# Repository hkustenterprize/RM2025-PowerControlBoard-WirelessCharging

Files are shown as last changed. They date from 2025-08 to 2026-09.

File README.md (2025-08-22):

<div align="center">

# RM2025-超级电容与无线充电系统开源
## 香港科技大学ENTERPRIZE战队

</div>

> 论坛链接：https://bbs.robomaster.com/article/761385?source=8

以下为复制论坛内容



大家好呀，RM2025的超级电容和无线充电的开源报告终于写完了，这套前前后后做了三四个月，最后在用在了所有上场的车上（无线充只有步兵和英雄有），场上没出过什么问题，很稳定。硬件上与上一代开源没有很大变动，主要的改动是超级电容换了**峰值电流内环**，然后与无线充电进行了融合，放到了一个MCU上去控。虽然有一些缺陷和不足但是总体效果还可以，希望可以帮到大家。如果大家有任何有疑问或者发现有问题的地方欢迎随时联系！

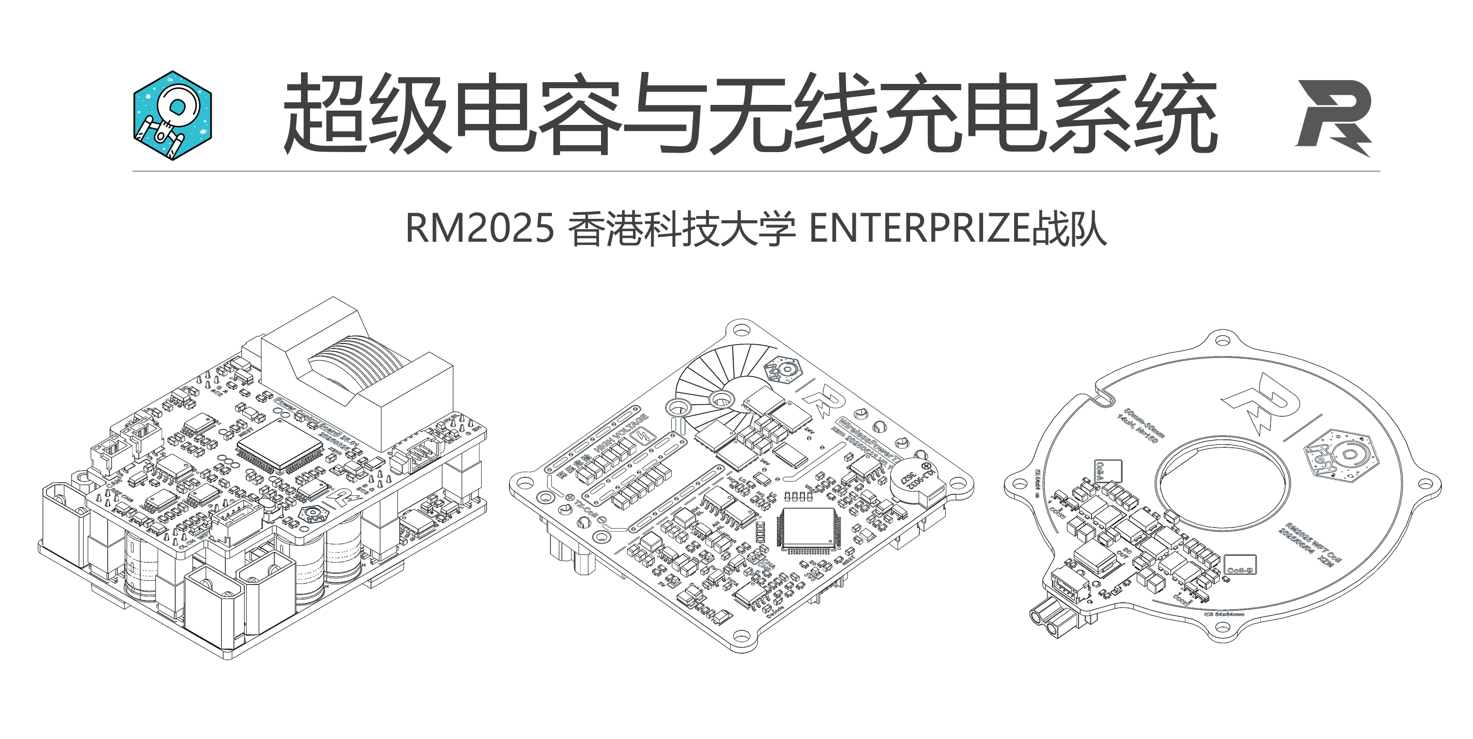
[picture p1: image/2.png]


> 欢迎加入开源交流QQ群：581184202

发射端/功控板硬件、功控板代码：xzm
> 联系方式：微信 xianziming0531，邮箱 zxianaa@connect.ust.hk

发射端代码：zzy
> 联系方式：微信 baoqi-zhong，邮箱 zzhongas@connect.ust.hk

## 前言

因为峰值电流调试起来比较复杂，也比较麻烦，所以大家有需要还是建议优先参考我们24年/23年的开源，这两版电容都是可以保证稳定的，24年的开源基本上板子做出了烧个代码就能用了。

硬件上整体改动不大，也是分了上下板的设计，下板加了一个用来无线充电的数控Buck，MCU换成了G474，为了峰值电流改了采样电阻的位置，然后根据写23赛季开源的学长的建议改了一下实现上管常开的方式，具体的东西都写在开源报告里了。

整体上场的效果还是不错的，电容响应很快，无线充电功率传输和反向通讯表现也很稳定（可惜复活赛输太快了没在比赛时充），今后有机会也会补充更多资料。无线充效果展示可以看 https://bbs.robomaster.com/article/760961 里面的视频。

## 工程文件

使用 KiCAD 8.0设计，可以点击下面的链接用 kicanvas 在线预览。

功控板上板：[<u>**点击预览**</u>](https://kicanvas.org/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)

功控板下板： [<u>**点击预览**</u>](https://kicanvas.org/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 )

无线充电发射端： [<u>**点击预览**</u>](https://kicanvas.org/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 )

无线充电接收端线圈： [<u>**点击预览**</u>](https://kicanvas.org/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 )

## 开源报告

见“技术报告” 文件夹

[**技术报告 PDF**](https://github.com/hkustenterprize/RM2025-PowerControlBoard-WirelessCharging/blob/main/%E6%8A%80%E6%9C%AF%E6%8A%A5%E5%91%8A/RM2025%E8%B6%85%E7%BA%A7%E7%94%B5%E5%AE%B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)

[**省流版 PDF**](https://github.com/hkustenterprize/RM2025-PowerControlBoard-WirelessCharging/blob/main/%E6%8A%80%E6%9C%AF%E6%8A%A5%E5%91%8A/%E7%9C%81%E6%B5%81%E7%89%88.pdf)

## 代码

功控板（超级电容+无线充电接收端）：待整理和测试，9月初整理过后的代码测好后开源

无线充电发射端：待整理，近期开源

## 相关开源
无线充电站机械结构：[ **【RM2025-无线充电站机械结构思路分享】香港科技大学ENTERPRIZE战队** ](https://bbs.robomaster.com/article/760961)

电容组：[**【RM2025-超小体积1980J电容组开源】香港科技大学ENTERPRIZE战队**](https://bbs.robomaster.com/article/760959)

## 复刻/已知问题/使用注意事项

1. 如果使用无线充电需要在功率控制板下板 无线充Buck的上管并联一个大功率肖特基二极管
2. 无线充电发射端的峰值检测二极管需要替换为肖特基二极管并联或其他快恢复二极管
3. 无线充电发射端的谐振电感需要自己绕，铁粉芯磁芯+利兹线
4. 使用手册和其他注意事项待完善，如遇问题欢迎随时联系

## 参考资料
1. 【RM2024超级电容控制器硬件+软件完全开源】 (史上最详细的开源！)香港科技大学ENTERPRIZE战队 https://bbs.robomaster.com/article/54127

2. 【RM2023-数控超级电容方案开源】香港科技大学-ENTERPRIZE战队 https://bbs.robomaster.com/article/9452

3. STM32 AN5306: Operational Amplifier (OPAMP) usage in STM32G4 Series

4. STM32 RM0440: STM32G4 series advanced Arm®-based 32-bit MCUs

5. STM32 AN5497: Introduction to the buck current mode with the B-G474E-DPOW1 Discovery kit（重要）

6. STM32 AN4539: HRTIM cookbook 

7. Qi Specification: Communications Physical Layer, Version 2.0 April 2023 

8. NXP AN4701: Demodulating Communication Signals of Qi-Compliant Low-Power Wireless Charger Using MC56F8006 DSC
STM32G474xB STM32G474xC STM32G474xE Datasheet 

## 致谢
感谢 ENTERPRIZE 战队硬件组学长 JYC RY OFR 为硬件部门打下的坚实基础，并在本赛季为超级电容与无线充电系统的设计调试中提供了巨大帮助

感谢 ENTERPRIZE 战队硬件组队员 ZZY 承担了大部分构建、调试发射端代码的工作

感谢机械组SJY帮忙画的保护外壳

感谢吉林大学、中国石油大学（华东）、华南理工大学在交流中分享的宝贵经验

非常感谢各位对香港科技大学 ENTERPRIZE 战队开源项目的关注与支持，若您在机器人设计过程中受益于我们的项目，恳请在开源引用中注明我们的项目来源。你们的支持是我们不断前行的动力。让我们携手共建一个鼓励创新、协作与超越的 RM 开源生态。







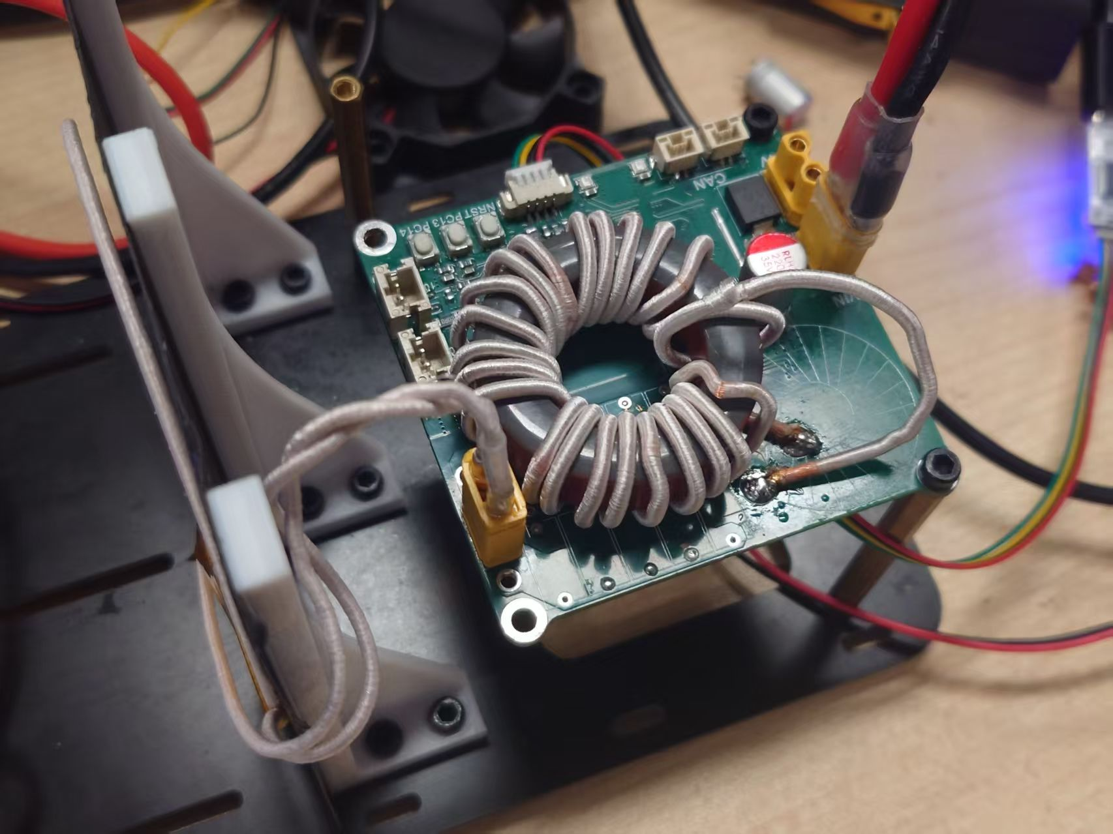
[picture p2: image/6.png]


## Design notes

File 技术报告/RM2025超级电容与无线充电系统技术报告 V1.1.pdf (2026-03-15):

1 / 96

# 超级电容与无线充电系统技术方案

RM2025 香港科技大学 ENTERPRIZE 战队

2026/03/16 V1.1

2 / 96

目录

3 / 96

开源报告版本：

V1.0 | 2025/08/08 | 首次发布
V1.1 | 2026/03/16 | 进行部分修正与补充，以 ** 标明

4 / 96

## 1. 技术背景概述

在 RM2025 的规则中，对于整车硬件要求大为提高。首先，总能量的限制的引入对电容控 制器的效率、响应速度等提出了更高的要求；其次，无线充电系统的加入使得底盘及超级电 容系统的架构变得更加复杂。

RM2025 赛季的一大变化是“能量限制”，与之前单纯的功率限制相比，能量限制对整车 设计要求再一次提高，从“开源”与“节流”两个角度分别来分析针对“能量限制”加入的 优化方法：

开源（增大可用能量）

- [硬件] 进行无线充电（在充电站以 120W 功率向电容组充入额外能量），详见“4. 无 线充电系统”
- [硬件] 提升比赛开始时的电容容量：例如比赛开始时电容组实际存入 1600J，实际可用

能量为 23000J+1600J=24600J，假设电容组的实际容量可以提升为 1900J，那么实际 可用能量也会相应提升，详见“3.6 超级电容组设计”

节流（减小能量损耗）

- [硬件] 进行动能回收，将刹车时的能量存入电容，详见“3.3.9 数字外环设计与实现”
- [硬件] 减小硬件损耗，如电容控制器、电容组、线损等等，在下文中将会重点讨论。详

见“3.2 硬件设计”

本文分为三部分探讨解决方案：整体硬件架构、超级电容系统与无线充电系统。

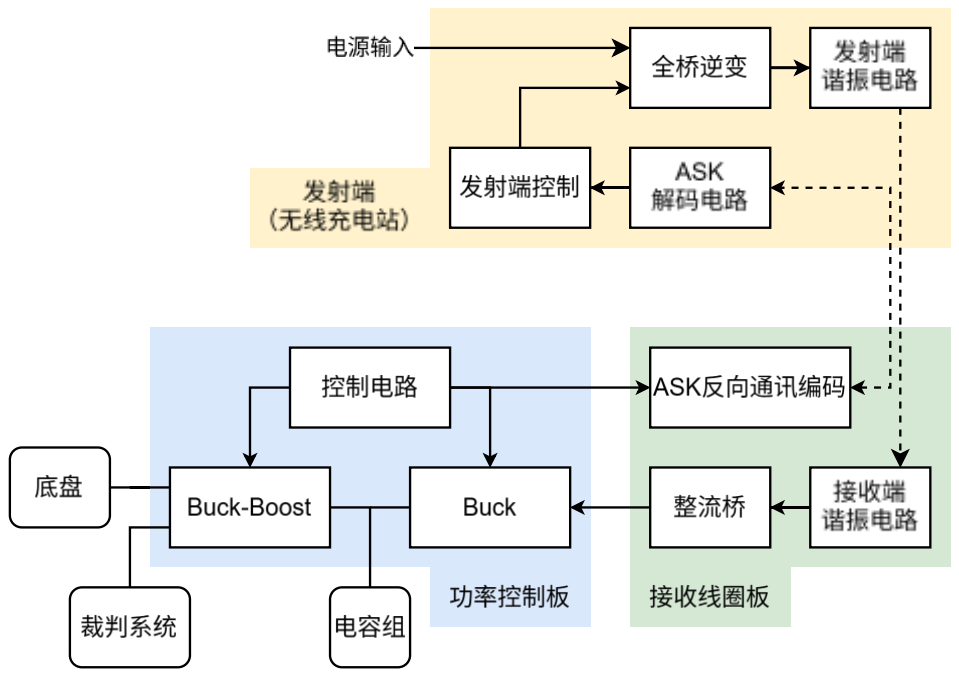
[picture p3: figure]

5 / 96

## ·2. 整体硬件架构

## 2.1 超级电容系统硬件拓扑

超级电容系统拓扑继续沿用上代电容控制器的双向 Buck-Boost 升降压架构，使得电容组 电压可以高于 等于或低于底盘电压，电容组最大电压值可以达到规则限制的 30V。由于电 容组电流受限于裁判系统超级电容管理模块 CM01 的 15A，所以电容组电压越高，理论最 大放电功率越大。以本设计中的 29V 电容组为例，其满电时理论最高可输出 435W 功率。

## 2.2 无线充电系统硬件架构

最大化无线充电系统的效率需要通过配谐来最小化无功功率，在 RM 场景下对无线充电系

统又以下要求：

- 无线充电系统的发射端体积可以较大，但接收端体积限制较为严格
- 在未对准时需要有较强的可靠性
- 发射、接收端间需要进行握手后进行充电
- 接收端需要能够处理 120W 的输入功率，并将其充入电容组中

在以上需求之外，为了简化硬件设计和接线难度，将无线充电接收端的相关电路与超级电容 系统融合，控制在同一块 MCU 上实现。

在考量上述因素并且查阅相关资料后，最终决定在功率传输部分使用 LCC-S 拓扑，激励源 选择全桥逆变，接收端的功率变换器选择 Buck 架构，将整流桥输出降压输入到超级电容中。

无线充电握手部分，选择通过模仿较为成熟的 Qi 协议的方法，通过 FSK 和 ASK 实现。

6 / 96

## 3. 超级电容系统

## 3.1 方案总览与主要创新点

峰值电流内环

25 赛季超级电容控制器的最大改变是实现了峰值电流内环控制，由模拟电路实现的峰值电 流内环理论上可以实现电感电流单周期达到设定峰值，配合简单的软件外环，其电流阶跃响 应可以达到 20us 级别。同时，纯模拟内环大大降低了 MCU 的运算负载，使得数字环路的 频率可以进一步提高，以实现更快的响应速度与更灵敏的保护。

峰值电流采样与平均电流采样共用放大器，最小化斜坡补偿

与峰值电流常见的在低位采样的设计不同，本设计在高位 MOS 处加入采样电阻进行采样， 将滤波电容放置于采样电阻后以采集电感电流。电流采样放大器输出直接连接到比较器的输 入进行峰值电流控制，同时也经过二阶低通滤波获得平均电流，并使用 ADC 采样用于软件 计算。这样的设计无需增加额外的采样电路，同时这样可以得到更多开关阶段的电感电流， 可以通过选择不同阶段的电流进行控制来最小化斜坡补偿的幅度。

充分利用外设简化电路

在具体实现上，得益于 STM32G474 的强大外设，硬件电路极为简化。峰值电流控制环路 的实现仅在电流感应放大器部分使用了 INA240A1 外置元件，剩余部分的环路，包括比较 器和 DAC 都在 MCU 内部实现；在电压检测中，通过使用 MCU 内置的运放的 Follower（跟 随器）模式，省去了外置运放，节约成本的同时简化了 PCB 布局。

充分利用外设减小软件运算量

在硬件层面外，25 赛季的超级电容系统充分利用 MCU 内部的不同外设间的互联矩阵，进 一步通过硬件外设替代软件计算。例如 OVP（过压保护）和 OCP（过流保护）通过 ADC 的 AWDG（模拟看门狗）实现触发保护，在进一步减小 MCU 的运算量的同时也加快了保 护的响应速度。在实际测试中，25 赛季超级电容系统的保护响应速度快于 24 年的设计，在 短路保护测试中尤其明显，短路产生的火花几乎不可见，且多次触发也不会损坏功率级电路， 证明了其优异的响应速度和稳定性。

无隔离电源上管常开

四开关 Buck-Boost 实现上管常开有助于提高转换效率。与使用隔离电源模块的传统做法不 同，25 赛季超级电容控制器的功率级利用拓扑本身的特性，使用了类似电荷泵的结构实现 上管常开，同时无需增加额外的控制芯片。无隔离电源的设计有助于减小静态功耗，使用隔 离电源模块时，静态功耗约为 2W，使用类似电荷泵的方式静态功耗仅有 0.8-1.2W 左右。

7 / 96

### 3.2 硬件设计

### 3.2.1 硬件设计总览

硬件上整体分为上下两块 PCB 板，上板为四层板，包含所有控制电路，下板为双层板，包 含超级电容和无线充电接收端的功率级，两板间使用 2.0mm 排针连接。

由于测试中发现下板功率级发热不大，故未采用铝基板，使得硬件设计更为自由（可以使用 直插电容、XT30 等通孔元件），并在板后粘贴一块 40x30x5mm 的散热片来辅助散热。将 发热网络（例如 MOS 管的 D 极）通过密集的过孔导热至 PCB 背面。

8 / 96

### 3.2.2 功率级

功率级为双向四开关 Buck-Boost 架构，分为 AB 两侧。本设计中将采样电阻放置于滤波电 容和高侧 MOSFET 间以对电感电流进行采样，当高边 MOSFET 打开时，采样电阻上的电 流等于电感电流，具体的峰值电流控制方式将在后文“3.3 环路与控制”部分详细介绍。

开关频率与电感选型

选择电感时，要在感值和饱和电流足够的情况下保证体积不会过大、且内阻尽量小。本设计 中电流双向流动，变换器的功率级一直处于 CCM 模式，控制上有四种工作模式（“3.3.6 时

序图”中详细说明），分别为 Buck、Buck-Boost(Vin<Vout)、Buck-Boost(Vin>Vout)、Boost。

定义 A 侧为输入端，由于 A 侧连接电管，电压范围即为电池电压范围，以使用 TB48S 为例， 电压最小为 22.2V，最大为 26.1V。B 侧为输出端，连接电容，电容电压范围为 0 - 30V。

选择开关频率为 250kHz，此频率下可以保证开关损耗不会过高、电感体积不会过大且不会 因为频率过高提升峰值电流控制的难度。适当大小的电流纹波会使得峰值电流控制更容易， 所以选取目标峰值电流为 4A 以内。

CCM Buck 模式下，电感电流纹波为: ∆IL =

Vout
L

(1 − DA

)

1
fs

=

Vin
Lfs

(1 − DA

)DA

当 DA = 0.5 时，∆IL 取最大值，Vin 最大为 TB48S 电池的 26.1V，因此：

∆IL,max =

26.1V
L×250kHz × 0.25, 令 ∆IL,max < 4A，L > 6.525uH

CCM Boost 模式下，电感电流纹波为: ∆IL =

Vin
L

(1 − DB

)

1
fs

=

Vin
L

(1 −

Vin

Vout

)

1
fs

当 Vout = 30V, Vin = 22.2V 时取得最大值：

∆IL,max =

22V
L×250kHz × (1 −

22V
30V

), 令 ∆IL,max < 4A，L > 6.96uH

CCM Buck - Boost 模式下，设计一侧占空比为 0.84，另一侧小于 0.84（后文会详细展

开），此时 Vout ≈ Vin ≈ 24V, 估算电感电流纹波为：∆IL =

24V
L

(1 − 0.84)

1
fs

令 ∆IL < 4A，L > 3.84uH

9 / 96

B 侧由于输出电流会受到裁判系统电容管理模块 CM01 的 16A 电流限制，实际最大电感电

流为 Boost 状态下 Vout = 30V,Vin = 22V 时取得，此时：

IL,peak = 16A × Vout⁄Vin + 0.5∆IL < 22.5A

考虑留有一定余量，选择电感饱和电流至少为 25A

最终，选择 10uH VER2923 电感，饱和电流 30 - 37A，DCR 约为 2.5mΩ，损耗较小，最 大电流纹波小于 3A，满足设计要求。

电容选型

选择电容时，假设最大电流纹波为 3A，由于 Buck-Boost 模式下电感电流波形近似为梯形， Boost 或 Buck 模式下近似为三角波，所以在电流纹波相同时最大电压纹波在 Buck-Boost 时取得（积分电感电流与平均电流的差值最大），可以估算输出纹波一定小于：

∆Vout <

T
2

×

Ipp
2

×

1

Cout

。

在采样电阻后每侧使用 4 个 10μF 50V MLCC 电容和 2 个 220μF 35V 固态电容分别进行低 频和高频滤波，此时输出纹波理论最大不超过 50mV，符合设计要求。

在 PCB Layout 时将高频功率环路（MLCC 电容 - 采样电阻 - 半桥 – 地平面）面积最小 化，并在保证过流能力足够的情况下最小化两侧 SW 的面积来减小干扰。

采样电阻选型

采样电阻选用 2mΩ 2512 的合金电阻进行电感电流，选型时主要有以下考量：

- 考虑损耗时，采样电阻不能太大。2512 电阻的最大功率为 3W，以最大电感电流 25A

计算，Rmax = Pmax Imax

2 ⁄ = 4.8mΩ，且相对 NMOS 内阻 (5.5mΩ) 不能太大

- 考虑采样时，采样电阻不能太小。采样电感电流需要较高带宽的电流感应放大器，而一 般放大倍数越大的放大器带宽越低、噪声越大，限制了放大倍数不能很大。由于 ADC 的精度限制，采样电阻阻值太小会导致分辨率过低。结合使用的电流感应放大器

10 / 96

INA240A1（选型在后文“3.2.5 采样与反馈”会提到）的 20V/V 放大倍率，最终选择

2mΩ的采样电阻。

最终 ADC 采样值理论计算公式为（ADC 分辨率 12bit）：

ADC Value = I × 2mΩ × 20 V⁄V × (4096⁄VREF)

理论分辨率和量程为 (VREF 取 2.9V) ：

Ires =

2.9V × 1
2mΩ × 20 V⁄V × 4096 = 0.0177A

Irange = ±

2.9V⁄2
2mΩ × 20V⁄V

= ±36.25A

功率 MOSFET 的选型

对于功率 MOSFET，要在保证 VDS 耐压余量足够的情况下，取得栅极电荷量、导通内阻间

的平衡。这里沿用 2024 赛季队内开源的选型 BSC066N06NS：其耐压为 60V，高于两倍最 大电压，防止电压过冲损坏 MOS；栅极电荷小于 20nC，保证较低的开关损耗并缩短死区

时间，防止在 VDS 较高时超过 SOA；Vgs = 10V 时 Rdson 为 5.5mΩ，损耗较小；持续电 流 64A、峰值 256A，远大于正常运行需求，保证了足够的安全余量。

其他设计

两侧滤波电容后各放置有一对 TVS+保险丝的保护电路，此电路可以在电流失控、输入输出 反接或过压等情况时熔断保险丝。保险丝选型为 1808 封装的 20A 快断保险丝，内阻约为

1.5mΩ。

A 侧在保险丝后有另一个 2mΩ 的采样电阻，用来采集裁判系统端的输入电流，此处虽然电 流更小（最大约为满级功率时 5A 左右），但是考虑到简化 BOM（防止错焊、减少备料种 类等）且分辨率足够的情况下保持相同的采样电阻和电流感应放大器的配置。

将采样电阻放置于保险丝后的设计可以保证即使在超级电容系统发生严重故障、保险丝断开 时，底盘也可以直接被裁判系统供电，且整个超级电容系统完全断开。

11 / 96

### 3.2.3 驱动级

栅极驱动芯片选型

栅极驱动芯片选用 UCC27201A 或者其平替 SLM27211。虽然 UCC27201A 性能稍弱于

UCC27211，但后者非常容易买到假货，且 UCC27201A 3A 的推挽能力在 250kHz、功率

MOSFET 栅极电荷不到 20nC 的已经足够，所以选用 UCC27201A 作为栅极驱动。后来经 过测试发现 SLM27211 稳定性足够且价格更便宜，于是在后续版本换用 SLM27211。

栅极驱动电路

栅极驱动电路以 UCC27201A 为核心，贴近 VDD 引脚放置一个 4.7μF 50V 电容，保证在开 关瞬间不会因为寄生电阻过大导致 VDD 电压突降而使芯片进入 UVLO 保护。在输出引脚 HO 和 LO 各串联一各栅极电阻，防止过快的开关导致电压过冲，此电阻需要通过测试反复 调整为合适的值，这里取 3.3Ω。自举电容按数据手册选用 100nF 0603 50V 电容。

布局中要尽量缩短高 di/dt 回路，尤其是栅极的走线要尽可能粗且短，输入电容要贴近芯片 的 VDD 引脚并保证地的连通性较好。

为了保证 MOSFET 的 Rdson 较小，设置驱动电压为 10.8V。过高的电压会使栅极电荷增大， 过小则会加大 Rdson，考虑到数据手册推荐电压为 10V 和高频开关中寄生参数的损失（上 管自举电容充电二极管的压降等），设计驱动电压为 10.8V

12 / 96

### 3.2.4 上管常开实现方式

在输出与输入电压有一定差距后，Buck 或 Boost 模式较比 Buck-Boost 更为高效，但如果 一侧上管直接常开，由于 G 与 S 级间漏电等原因，上管会渐渐转为不导通状态，所以要实 现上管常开必须采用一定方法保持上管栅极电压不变。

现有方案参考

队内 2023 和 2024 赛季的解决方案为引入两个隔离电源模块，输入为 10.8V 和 GND，输出 负连接到 SW，正连接到 HB（自举电容两侧），这个方案的优点是设计较为简单，但是即 使隔离电源输出电流很小，也会有较大的静态功耗（在本赛季这个问题会被放大）。

另一种解决方式是在上管常开一侧以较低的频率进行开关充电，例如对侧开关 500 次，常 开侧进行一次占空比为 0.95 的开关，并配合增大的自举电容实现上管近似常开。这种方案 的优点是没有引入额外的静态功耗，且无需额外硬件上的改变，但是软件上实现较为复杂。

本系统使用的新方案

在本方案种则使用了一种类似电荷泵原理的方式实现上管常开。如图，其中 BAV99 为 100V 耐压、SOT-23 封装的开关二极管（其实就是两个二极管合在一起），BZT52C11S 为齐纳 电压为 11V±0.6V 的稳压二极管，两个 10kΩ 电阻为限流电阻。输出连接到自举电容两端。

** 此处 R11 的阻值建议修改为 33ohm 左右，防止充电不足

此电路工作原理主要依赖一个特性：常开侧对侧的电路一定在进行开关，例如 Buck 工作时

A 侧进行 250kHz 的开关，B 侧常开，Boost 同理。

原理分析

以如图 Boost 工作、输入电压 24V、输出电压 24V（理论上最不理想的电压）需要 A 侧上 管常开时为例，工作分为两阶段：

B 侧下管打开，此时 B_SW 为 0V，电容 C12 通过 R11 电阻与 D11 左侧二极管充电，

此时 D11 右侧的二极管截止。在稳态运行中，C12 的电压为 10.8V – 0.8V = 10V。

B侧上管打开，此时B_SW为24V，A_SW为24V，C12上端电压约为24V + 10V = 34V， 此时如果自举电容电压较低，则 C12 通过 D11 右侧的二极管与 R12 电阻向自举电容充 电，同时通过稳压二极管限制自举电容两端电压为 11V 左右，稳态运行中自举电容可

13 / 96

以至少可以被充电至 9.2V 左右，即高侧开关 Vgs 至少会保持在 9.2V 左右。

不考虑漏电，实际运行中因为常开侧电压一定小于开关侧，且差距一般至少为 2V（否则进 入 Buck-Boost 模式），常开的上管的 Vgs 一定可以维持到稳压二极管的电压（11V 左右）。

漏电与充电理论计算

上管常开时，栅极漏电的来源有 (1)MOSFET 本身 (2)稳压二极管 (3)自举电容 (4)驱动芯

片，经查阅数据手册，其最大值分别为 (1)100nA (2)0.1μA (3)~5nA (4)1μA，加和为μA 级 别，且驱动芯片正常漏电为 0.0005μA，与最大值相差较多，实际漏电电流远小于估算值。

正常运行时，假设 C12 两端电压为 9.9V，自举电容两端电压为 9.0V，开关二极管压降为 0.8V (10mA)，则单次开关的充电能力为（两阶段一致）：

Q = ∆V (1 − e
−

t

RC) C = (10.8V − 0.8V − 9.9V) (1 − e
−

2μs
4.7μF×10kΩ) × 4.7μF ≈ 0.02nC

此时平均充电电流 I ≈

0.02nC
4μs

≈ 5μA 大于漏电流最大值，由于估算条件极为保守，实际充电

电流会显著大于估算值。

静态功耗分析

估算静态功耗时，假设自举电容稳定在 10V，充电电流忽略不计，功耗近似为：

PDC = |VA − VB

| × (|VA − VB

| − 11V)⁄20kΩ

可以看出最大静态功耗为 A 侧 24V B 侧 0V，电容刚刚开始充电的场景，此时功耗约为 0.016W 且只有单侧上管常开电路有功耗，在正常运行电压范围（B 侧 10-30V）时静态功 耗极低，仅有 mW 级别，可以忽略不计。

结论与实际测试

综上所述，本电路理论上可以十分稳定且低功耗地实现上管常开，实际测试中栅极电压可以 稳定在 10V 左右。Buck 和 Boost 状态下都可以稳定运行。对比隔离电源模块的方案，25 赛季采用的新方案使得整体静态功耗从 2W 降低到 0.8W-1.2W 左右，并缩小了元件所占体

积。

14 / 96

### 3.2.5 采样与反馈

总体需求分析

超级电容系统中，需要采集 5 个物理量作为控制依据，分别为：两侧电压 VA、VB，两侧电 流 IA、IB，裁判系统端电流 IR。其中两侧电流需要特殊处理，峰值电流需要电感电流的波

形，而 ADC 需要采样其平均电流。

为了提高响应速度，软件外环的运行频率为 62.5kHz (开关频率/4)，每开关周期一采样，所 以需要采样电路滤波有较高截止频率。数控电源滤波频率一般取开关频率的 1/10 到 1/20， 考虑到提升响应的需求，适当选择较高频率，接近 25kHz 左右。

由于 STM32 的 ADC 采样时近似于给一个小电容充电，所以如果条件允许则在 ADC 引脚前 放置一个小电容，防止采样时间过短产生误差，或使用运放进行跟随来减小阻抗。

参考电压

采样电路与 ADC 需要精确的参考电压以保证结果的稳定与一致。如果直接使用 LDO，即使 在进行校准后也无法避免温度和输出电流等因素导致的电压漂移。所以在本设计中使用了 STM32G4 系列内置的电压参考，省去了独立的参考电压芯片。

STM32G4 系列内置高精度电压参考，有 2.048V 2.5V 2.9V 三个电压挡位，本设计中选用 2.9V 挡位，其精度标称为±4mV，理论精度 0.14%，意味着测量功率时由参考电压造成的

误差最大为 0.276%。

为了给电路感应放大器提供参考电压，将 MCU VREF+引脚输出的
参考电压经过 MCU 内部运放跟随后的输出作为参考电压输出，同 时在 VREF+引脚和最终输出的 VREF 网络都使用电容进行滤波和

稳压。

电压采样电路

电压采样首先使用 33k 和 2.2k 电阻分压，与 3.3nF 电容组成一阶滤波，设计参数如下：

直流缩放倍率：GainDC =

2.2kΩ
2.2kΩ+33kΩ

=

1
16

V⁄V

最大量程：Vmax = VReference⁄GainDC = 2.9V × 16 = 46.4V

一阶滤波截止频率：fcutoff =

1
2πReqC

=

1
2π(33kΩ∥2.2kΩ)×3.3nF

≈ 23.38kHz

ADC 理论分辨率：Vmax⁄4096 = 11.328mV

滤波后的信号进入 STM32G4 内部运放的输入，内部运放配置为 Follower 模式，并将运放

输出连接到 ADC 输入。内置运放的 Power Mode 配置为 High Speed，可以提供 45 V/µs 的压摆率，更适合处理高频模拟信号。

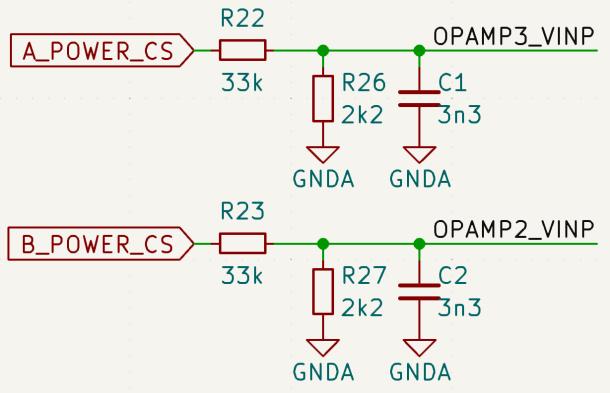
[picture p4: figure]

15 / 96

电流感应放大器的选择

峰值电流控制需要获得波形较为精确的电感电流，这就对采样带宽提出了很高要求，而其电 流绝对精度要求不高，所以选择放大器时基本仅需重点关注带宽和压摆率（例如 LM51770 的电感电流采样放大器带宽为 1Mhz），配合低位采样即可较好地获得相对精确的电感电流 波形。而 ADC 采样的平均电流对带宽要求不高（一般为开关频率 1/10 到 1/20 左右即足够）， 但却对绝对精度要求较高，选择放大器时需要重点关注误差、漂移和噪声抑制等参数。同时， 由于电流双向流动，需要选择支持双向电流采样或带有 VREF 引脚的电流感应放大器。

综上所述，本方案的做法虽然电路简单，但是对电流感应放大器要求较高，需要同时具备高 带宽、高共模电压、低误差、低漂移和噪声抑制等特性。由于符合要求且带宽 800kHz 以上 的电路感应放大器价格较高（例如带宽 1.1Mhz 的 INA241A1 价格接近 20 元/片），所以在 测试 INA240A1 后发现其带宽足以稳定实现峰值电流控制后，选用其作为电流感应放大器。

INA240 系列共有 A1-A4 四种型号，为了减小噪
声，选择增益为 20V/V、标称带宽为 400kHz 的
A1 型号。通过数据手册中的增益-频率图可以看出

在 1MHz 频率下 INA240A1 仍可以保持 10dB 的 增益，由于峰值电流控制并不需要增益很准确的
高频信号，故其可以稳定实现峰值电流控制，与
测试结果相符。

16 / 96

电流采样电路

峰值电流控制模式需要对电感电流进行采样，使用上文提及的 2mΩ 电阻，在上板使用 INA240 电流感应放大器将采样电阻两端差分电压转化为单端电压输出。电感电流信号连接 比较器进行峰值电流控制，同时经过二阶 RC 滤波得到平均电流并通过 ADC 采样以进行软 件环路控制。

与将电感电流采样与平均电流采样分离的设计不同（如 LT8705 等），本方案的设计可以通 过单一电流感应放大器同时获得电感电流与平均电流。这种做法很大程度上简化了电路，核 心部分仅需两个电流感应放大器，并且无需引入额外的采样电阻，减小了损耗。

通过第一版硬件的测试发现一阶 RC 滤波的 ADC 采样结果噪音较大，所以在第二版中使用 了二阶 RC 滤波，可以实现在截止频率后-40dB/dec 的衰减。参考电压源分别连接到 2.9V 的参考电压和模拟地，实现 1/2 参考电压的输出偏置以实现双向电流检测。具体理论设计参 数如下：

直流缩放倍率：GainDC = 2mΩ × 20V⁄V = 0.04V⁄A

单向最大量程：Vmax = 0.5VReference⁄GainDC = 0.5 × 2.9V⁄(0.04V⁄A) = ±36.25V

二阶滤波截止频率： fcutoff ≈

1
2πRC

=

1
2π×2.2kΩ×3.3nF

≈ 21.92kHz

ADC 理论分辨率：2Vmax⁄4096 = 17.70mA

17 / 96

对于裁判系统电流采样，由于其采样直接为平均电流（采样电阻两侧均有滤波电容），噪音 较小，故使用一阶 RC 滤波即可得到噪音较小的数据，其余参数与上文一致。

模拟电路 PCB 布局

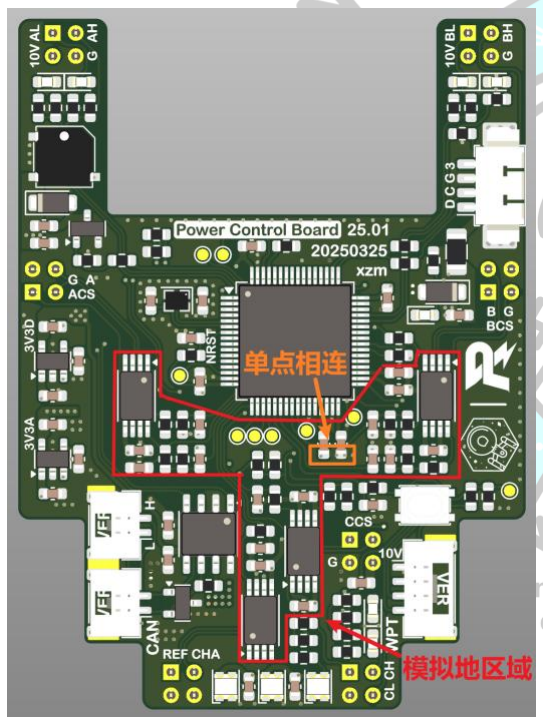
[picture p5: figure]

由于超级电容的 PCB 上同时由敏感的模拟采样电路、数字电路和大功率的功率开关电路， 对 PCB 布局由较高要求。首先电容控制器分为上下两板，将大功率地和数字地进行了分割； 在上板上对模拟部分的地做了分割，并在 MCU 的 VDDA/VSSA 滤波电容处单点相连。

18 / 96

对于电流采样，差分信号线从采样电阻开始使用开尔文接法，通过排针来到上板并继续保证 等长差分，同时保证其不与相同网络其他处有连接，保持由采样电阻到放大器完全独立。

对于电压采样，由于排针体积 Pin 数的限制，在板对板连接处辅助供电输入端共用同一引脚， 在上板排针焊盘处分离，分别走向电压采样电路和辅助电压输入。

校准
尽管前文提到的各种设计已经尽量消除误差，但由于各种因素（例如 ADC 精度、温度、放 大器误差等）导致的误差仍然不可忽略，所以使用一次函数对 ADC 采样结果与真实值对比 进行拟合，实测可以极大提升采样精度。例如下图为采样电压的校准拟合：

实际使用中对每个焊接的电容控制板的五个测量量分别进行校准，校准结果统一存储在

Calibration.hpp 文件中，并根据 MCU 内部的 96 位 UID 进行编号，保证任意电容控制板只 需要进行一次校准且不会因为烧错代码使用错误的校准信息。

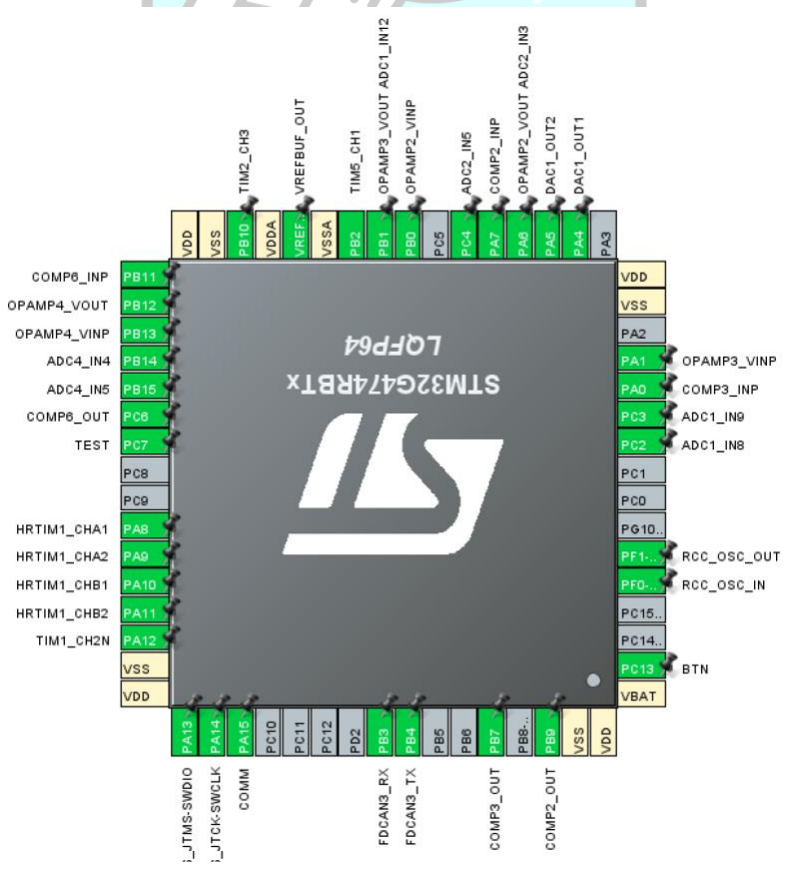
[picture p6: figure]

19 / 96

### 3.2.6 MCU 与控制

MCU 选用 STM32G474RBT3。STM32G474 提供了功能极为丰富的高精度定时器（HRTIM V2），使得峰值电流控制成为可能；170Mhz 的主频也使得环路计算可以更快；丰富的模拟 外设（电压参考、内置运放、比较器、DAC 等）使得外围电路得到极大简化；同时，选用 RBT3 版本使得其耐温达到-40°C 到 125°C，提高稳定性。

MCU 采用 LDO 供电，并在每个供电引脚配备 100nF 电容。晶振选用 2012 封装的 25Mhz 晶振以减小体积和干扰，PCB 上对晶振本身和其走线进行了包地处理、并在所有层禁止其 他走线来防止干扰。

由于实际使用中对于 BOOT0 和 NRST 按钮需求极小，故移除独立按钮，仅保留下拉与上 电复位电路。保留一个连接到 GPIO 的按钮进行交互。

STM32CubeMX 中的部分引脚配置如下（不包含无线充电部分）：

20 / 96

### 3.2.7 辅助供电

电源框图

超级电容及无线充电系统共有三个电压源，分别为底盘端电压、电容组端电压、无线充电输 入端电压。为了保证任意电压源有输入时系统都能工作，使用三个二极管分别从三个电压源 指向辅助供电 Buck 的输入，因为辅助电源功率很小，使用普通肖特基二极管即可。同时为 了烧录及调试方便，将 SWD 的 3.3V 输入通过保险丝和 TVS 保护后通入 3.3V 网络。

辅助电源电源网络

电源网络名称 | 描述 | 用电器
10V | MOS 栅极驱动电源 | MOS 栅极驱动芯片
5V | 5V 主供电 | CAN 收发器、蜂鸣器、LDO 等
3.3V | 3.3V 主供电 | MCU、CAN 收发器
3.3VA | 模拟 3.3V 供电 | MCU VDDA、电流感应放大器

取电位置

虽然辅助电源的功耗较小，但其电流仍然不可忽视，所以需要选取合适的取电位置来避免对 功率级电流测量的干扰。如图为超级电容系统功率电电路的框图：VREF 为裁判系统电源管 理模块的 Chassis 接口输出，通过裁判系统电流检测电阻后输出到底盘；底盘网络通过保 险丝进入 Buck-Boost 电路的 A 侧，在通过两个电流检测电阻、功率级后再经过保险丝进入 电容组。

实际辅助电源的 VA、VB 输入分别接入如同所示中的 VA_CS 和 VB_CS 网络。对于 A 侧， 在 VA_CS 处取电可以避免辅助供电输入绕过裁判系统电流检测电路，使得测得的裁判系统 功率不准。不在 VA 和 VB 处（采样电阻后）取电可以避免随功率级的电流采样造成干扰。

21 / 96

Buck 部分电路

Buck 芯片选用 RY8411。输入电压最高 42V，可以保证在功率级电压不超过 30V 的情况下 有充足的余量；输出电流最大 1.2A，远超辅助供电的需求；同步整流可以提供较高的效率

并且无需续流二极管、减小了电路面积。

输入部分采用三个耐压 40V，最大电流 3A 的肖特基二极管（K34），并且在经过 1A 的保 险丝后进入 Buck 芯片的输入；其中无线充电输入端（C_POWER）独立使用一个保险丝是 为了布局方便。每个 Buck 芯片输入各使用两个 1206 封装耐压 50V 的 10uF 电容，输出各 采用三个 0805 封装耐压 25V 的 22uF 电容，由于 X7R/X5R 材质的电容实际容值随着两端 直流电压的升高而降低，所以选用高耐压电容来减小容量衰减。电感选用 3015 封装的 4.7uH 电感，虽然其 DCR 较大（约为 100mΩ级别）且饱和电流较小（约为 1.1A），但对于辅助 供电来说已经足够。

22 / 96

布局上将全部功率回路在顶层布局完成。保证输入电容 - 芯片 - 输出电容的 GND 回路阻 抗较小，且输入电容距离芯片的 VIN 和 GND 尽可能近；自举电容高频回路紧挨芯片的 SW 和 BST 引脚减小干扰，电感布局保证 SW 的网络面积尽量小防止干扰；反馈回路在输出电 容后通过内层独立走线连接至采样电阻处，且保证 FB 网络面积尽可能小避免干扰。

LDO 部分电路

LDO 选用 RS3236，输入电压最大 7.5V，输出电流最大 500mA，都有较大余量。电路基本 参考数据手册，在 BP 引脚连接 10nF 电容来减小输出噪声。

PCB 布局上依然在同一层完成了功率回路的走线，保证输入和输出电容的两端离芯片尽量 近，为了防止 EN 引脚走线切割 GND，将其从内层接入芯片。

SWD 电源输入

由于电容控制器烧录及调试代码频率较低，对于 SWD 供电的处理和保护较为简单，通过 1A 保险丝和 3.3V TVS 进行防护，并使用一个 4.7uF 电容进行滤波。

23 / 96

### 3.2.8 通讯与交互

通讯部分采用 CAN 协议，直接接入底盘的 CAN 网络并与主控板进行通讯。收发芯片选用

SIT1042T/3，输出采用 ESD1CAN 进行防护。

交互上使用一个按钮进行重启和清除故障等操作，通过 WS2812B 进行状态指示。按钮使用 一个 RC 滤波电路来消抖，引脚使用 GPIO 内部上拉。WS2812B 选用 2020 封装减小体积。

### 3.2.9 成本控制

为了节约经费，超级电容控制器在设计上进行了最大程度的精简，例如前文提到的用 MCU 内部运放代替独立运放芯片等。同时，对于电阻或电容取值较宽松的地方进行了取值的统一， 在不同电流采样处统一采样电阻和电流感应放大器的选型，最大程度简化 BOM。 本赛季考虑全阵容+备车+备件的需求大致需要 8 套电容控制器，使用嘉立创经济型 SMT 贴 片核心板的电阻电容，其他元件和下板全部手焊，可以控制整套控制器成本在 100 元左右。

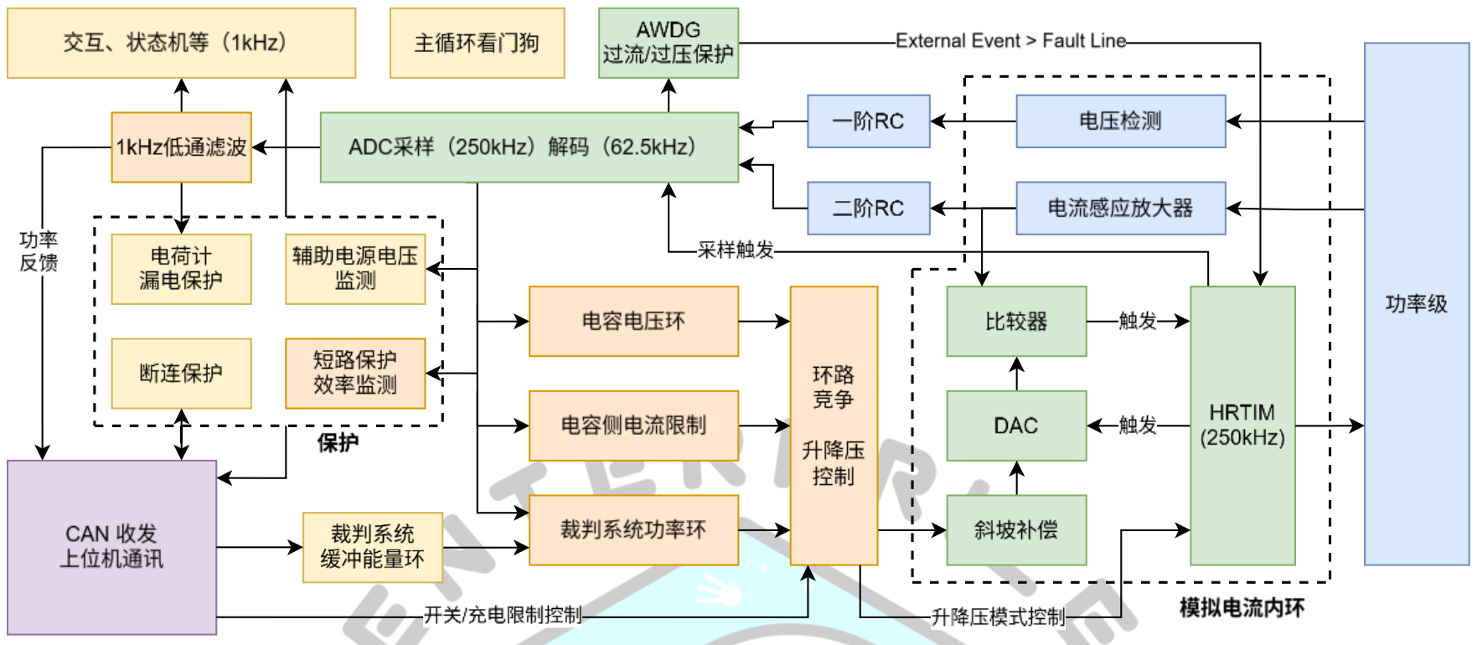
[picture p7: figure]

24 / 96

## 3.3 环路与控制

### 3.3.1 整体控制框图

如图，本方案使用 STM32G474 作为整体控制核心。其中使用了大量 MCU 内部外设来简化 硬件设计、加快软件运行速度。

### 3.3.2 控制系统整体需求分析

本部分主要基于 Buck-Boost 拓扑分析 RoboMaster 竞赛场景中超级电容系统的控制需求。 如图为简化的功率级框图，整个控制器共有三个功率端口，分别为：
- 裁判系统电源管理模块 Chassis 接口输出（下文简称 Referee/R 端）
- 底盘电机输出接口（下文简称 A 端）
- 电容组接口（下文简称 B 端）

在下文中将从限制因素入手，分析理想中的控制效果及实现方式。

25 / 96

限制因素

对于裁判系统 R 端（0V 或电池电压）：

- 比赛规则限制此接口输出的功率上限，功率计算方式为 R 端的电压×电流，其中电压为 电池电压，此功率上限一定不能超过，否则会导致判罚。
- 由于裁判系统电源管理模块无法检测负功率（不会返还反向流入裁判系统的能量），所 以理想情况下要保持此接口功率一直为正，即保证此接口只会输出能量。
- 虽然有功率限制的存在，但理想情况下控制器需要有完全吃满裁判系统功率限制的能力 以保证性能。

总结：R 端一定要保证不超过功率限制，最好保证功率不倒灌，最好可以吃满功率，电压输 入范围为电池电压

对于底盘端（与 R 端电压一致）：

- 此端口功率受上位机控制的电机决定。
- 此端口的瞬时功率较大，例如电机急停时会有巨大的反冲功率灌回系统中，系统必须反 冲有较强的处理能力，否则其将不受控制地流回电池，造成浪费。

总结：底盘端会承受较大瞬时功率，且系统无法控制接口的输出输入能量

对于电容组端（0V-电容组最大电压）：

- 此端口电压绝对不能超过电容组的最大电压，需要严格限制并保护。
- 由于此接口与裁判系统电容管理模块 CM01 直接串联，此端口的电流不能超过 CM01

的电流限制（±15A）。

- 此接口电流不能超过电容组最大充放电电流，并且在电容电压较低时需要进一步限制电 容组的充放电电流。由于电容组的最大电流一般很大（30A 级别），远大于 CM01 的限 制，所以这里只需要考虑低电压限制电流的情况

总结：电容端需要有严格的电压电流限制，并且在电容组电压低时要进一步限制电流

对于功率级本身，任意时刻电感电流不能超过饱和电流（约 30A 级别）

26 / 96

工况分析

| 底盘需求功率低 | 底盘需求功率高
电容能量低 | 快速充电 | 提供尽量多的功率，但优先保护 系统本身不会损坏
电容能量高 | 保持电容能量 | 提供尽可能高的爆发功率

除了一般工况，还有一些特殊情况需要考虑：

- 正常运行时电机可能会有反向功率（如刹车或下坡时），此时系统理想情况下可以回收 这部分功率，并且电容要留有余量来接收这部分能量。
- 即将无线充电时，为了充入尽量多的能量，需要将电容能量放电至较低水平，具体做法 为令底盘优先消耗电容组中的能量（闭环裁判系统功率为一个较低的值）。

控制方式实现

假设 Buck-Boost 效率较高并可以忽略其他损耗，那么三端口能量守恒，定义 R 端输入为正，

Chassis 端输出为正，Cap 端输出为正：

PR = PCℎassis + PCap

由于 R 端和 Chassis 端电压一致（忽略采样电阻压降），且都为电池电压：

VBATIR = VBATICℎassis + VCapICap → VBAT(IR − ICℎassis) = VCapICap

其中电池电压 VBAT 由电池电量决定（22V-26V 左右），不可控；电容组电压 VCap 取决于 电容组的能量，也不可控；ICℎassis 由电机需求决定，不受电容控制器控制。所以在底盘功

率需求波动时（即 ICℎassis 波动时），需要根据需求控制 ICap 来保证 IR 不超过

PLimit⁄VBAT ，且最好一直为正。同时，控制器也需要保证电容组电压 VCap 不超过一个限定
值。

27 / 96

### 3.3.3 纯数字控制模式分析

本部分主要参考队内 2024 赛季的开源：

【RM2024 超级电容控制器硬件+软件完全开源】 (史上最详细的开源！)香港科技大学

ENTERPRIZE 战队 https://bbs.robomaster.com/article/54127?source=4

控制逻辑框图

功率级分析

对于同步四开关 Buck-Boost，两侧的占空比直接作用于两侧电压的比值：

假设两侧占空比为 DA 和 DB，电压为 VA 和 VB，下管不会同时导通，工作在 CCM 模 式下，电路共有三个工作状态，根据伏秒平衡：

(VA − VB

)(DA + DB − 1)T + VA

(1 − DB

)T + (−VB

)(1 − DA

)T = 0V ∙ s

→ VADA = VBDB

其中 DA 和 DB 取值可以为 1（分别对应 Boost 和 Buck 模式）

根据不同的占空比分配方式，例如持续处于 Buck-Boost 模式或根据占空比需求在 Buck Buck-Boost 和 Boost 模式间进行切换，可以直接通过一个输入量控制电压比值

D = VB⁄VA = DA⁄DB

当需要控制电压时，可以直接通过增量式 PID 控制目标占空比。

当需要控制电流时，由于电路各处寄生电阻的存在，较小幅度地控制占空比即可控制电流。

28 / 96

控制逻辑简述

纯数控超级电容控制器的核心逻辑是裁判系统功率（电流）环与电容组电压环进行竞争，并 进行增量式控制。

具体实现上，两个控制环路使用增量式 PID 实现，裁判系统电流环的目标值为 “裁判系统功 率限制÷底盘电压”，结果在 “功率级 A 侧电流”的目标值上累加，电容组电压环 1 目标值为

优势与不足

数控超级电容系统的主要优势是软件、硬件设计都较为简洁，控制逻辑较为简单，并且通过 做好保护很容易实现很高的稳定性。例如队内 24 赛季开源的超级电容控制器在场上从未出 现故障。并且纯数控方案调试比较容易，仅需做好软硬件的配置，并调整软件环路参数即可 达到较好的控制效果。

然而，纯数控方案在现有基础上提升响应速度基本只能靠提升环路速度来实现，而加快环路 速度极大地受到 MCU 运算速度的影响，例如在本赛季初经过测试，在保留最小程度的保护 功能的前提下，STM32G474 可以实现开关频率 1/2 周期的环路运算速度（约 136kHz）， 但此时中断负载极高，使得其它功能的代码的运行受到极大干扰。数控方案提升环路速度同 样受到采样带宽的限制，更快的环路运算速度需要提升采样带宽，由于需要采样的量为平均 电流，提升采样带宽也会导致噪声和误差的增大。

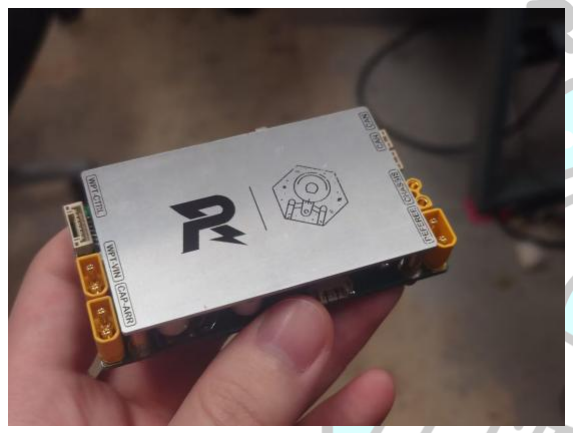
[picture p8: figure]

29 / 96

综上所述，新赛季的规则间接对超级电容系统的响应速度提出了较高要求，在本赛季初进行 了一系列尝试后，发现数控方案提升响应速度较难，例如下图展示了本人在赛季初设计的第 二版数控电容的测试版（包括无线充电部分电路）

所以，在尝试了解更多 DC-DC 控制模式相关知识后，决定对峰值电流模式控制进行探索与 尝试，通过底层控制方式的改变来达到提升响应速度的目标。

30 / 96

### 3.3.4 峰值电流控制模式介绍

峰值电流模式（Peak Current Mode Control）的核心是直接将电流波形用作 PWM 生成比 较器中。本部分将以 Buck 变换器为例，简要分析峰值电流控制模式。

本节主要参考了 STM32 的应用手册 AN5497: Introduction to the buck current mode with

the B-G474E-DPOW1 Discovery kit

典型电路框图（截取自 AN5497）

控制方式

如上图所示，控制器最终目的为输出恒定电压，并由电压外环控制峰值电流内环，由于在 RoboMaster 竞赛超级电容系统的应用场景下，大多数时间都在控制电流，所以本部分将主 要关注电流内环的实现方式。

峰值电流控制硬件上最大的不同是加入了电感电流采样。电流采样值输入到比较器的一个输 入，另一个输入由外环决定；比较器的结果输出到 SR 锁存器的一个输入，另一个输入为固 定频率的时钟源。

具体运行方式如下，参考时序图：

- 周期开始，时钟信号触发 SR 锁存器的 Set，SR 锁存器输出为高，Buck 功率级的上管

31 / 96

打开，电感电流开始上升。此时电流斜率为 (Vin − Vout)⁄L

- 当电感电流上升到目标峰值（由外环提供）比较器输出为高电平
- 比较器输出为高电平，触发 SR 锁存器的 Reset，此时 SR 锁存器输出为低，上管关闭
- 上管关闭后，下管打开（或续流二极管导通），电感电流开始下降，此时电感电流下降 斜率为 Vout⁄L，直到周期结束

主要优势

峰值电流模式最大的优势是电流响应速度极快。由于占空比不是由控制器决定，而且直接由 导通时间内电感电流的上升决定的，只要阶跃值小于电流纹波，电感峰值电流可以在单周期 内达到目标峰值。而根据电感大小、开关频率和占空比可以计算电感电流的峰峰值 Ipp，通

过 Ipeak = Iaverage + 0.5 × Ipp，可以通过目标平均电感电流计算出对应需要设定的峰值电
流目标，也就是说外环可以直接通过设定比较器负输入的电压来直接控制电感电流。

峰值电流模式的另一优势是可以严格限制峰值电流，从而最大程度减小过流风险。通过上段 相同的方法，由于 Ipp 一般不会剧烈变化且可估算，所以可以通过此方法限制正向或反向 电流，适用于电流双向流动的场景。

由于峰值电流环的运行只依靠硬件，无需任何软件的参与，这可以节省非常多计算资源，这 使得超级电容控制器拥有了一个无需很多计算资源（仅需进行模式切换）且响应极快的内环。

次谐波震荡

虽然峰值电流控制带来了极快的响应，但也为控制带来了更多挑战。其中最显著的问题是次 谐波震荡。如下图所示（截取自 AN5497），当上升端斜率 < 下降段斜率时，电感电流波 形会发散，并使得占空比抖动，最终呈现为“大小波”的现象，即一个周期占空比极大，下 一个周期占空比极小。对于上文所示架构的 Buck 电路，理论上此现象会在占空比大于或等

于 50%的情况下。

32 / 96

为了解决此问题，需要引入“斜坡补偿”，即通过给比较器输入增加斜率来补偿上升斜率过 小的问题，且占空比越大，需要的斜坡斜率越大。

电流准确度

虽然如上文提到，峰值电流与平均电流的关系可以通过理论计算得到，但是叠加斜坡补偿斜 率和噪音的影响，使得计算出的值与实际相差较大。对于一般的 DC-DC 变换器，峰值电流 限制不需要很准确，但是在超级电容的场景下需要较为准确地闭环电流，所以需要引入数字 外环来通过 ADC 采样出的平均电流对内环进行控制（或校准）。

其他问题

除了上文提到的影响较大的问题，峰值电流控制需要较高的电流测量带宽（如上文提到的 INA240A1 选型部分），并且由于模拟信号较多，对 PCB 布局有更高的要求。

33 / 96

### 3.3.5 峰值电流 Buck-Boost 硬件架构

对于 RoboMaster 超级电容控制器场景下，需要实现电压升降与电流的双向控制，结合上文 提到的 Buck-Boost 架构，需要详细分析需求来降低峰值电流控制的不足带来的影响并且最 大程度发挥其优势。在本设计中通过调整 SR 锁存器、比较器处的逻辑，最大化降低了斜坡 补偿的需求，并保证了不同模式间的平滑切换。

如上图所示，对于 Buck-Boost 架构的控制，使用两套峰值电流环路，使用 INA240A1 作为 电流感应放大器进行高位采样，采样电阻位于上管 D 极与输入/输出之间。当上管导通时， 通过采样电阻的电流即为电感电流。

每个 SR 锁存器有一个 Reset 源和两个 Set 源，Reset 源被固定频率的时钟触发，S0 被比

34 / 96

较器触发，S1 的作用是做占空比保护或屏蔽比较器输入从而实现固定占空比或上管常开。 具体实现方式将在下文“3.3.7 MCU 外设配置”部分详细说明。

接下来将通过分析不同升降压模式下的时序图来详细介绍控制方式，整个功率级一直工作在

CCM 模式下。

最小化斜坡补偿

对于斜坡补偿的需求，由于理论上至少有一半的占空比会出现次谐波震荡，所以最好可以令 功率级工作在理论上无需斜坡补偿的区间（50%-200%）（详见“3.3.6 时序图”），以此 减小斜坡补偿的需求和影响。

控制器 A 侧的电压为电池电压，B 侧为电容组电压，电容组的能量计算方式为：

E = 0.5 × C × U

2

假设电容组最高电压为 29V（详见“3.6 超级电容组设计”），那么电容组在 10V 时仅存 有 11.9%的能量，且此时受到电压限制，放电功率极大受限，所以在电容控制器控制算法中 设定 10V 为低压保护的阈值，电容组电压小于 10V 时控制器会逐步限制电容组电流至很低， 在 5V 左右彻底关断输出。

所以，可以认为电容组绝大多数时间都工作在 10V-29V 的区间，假设电池电压在 21V-26V 的区间内，可以算出最小占空比为 38.5%，最大占空比为 138.1%，大部分覆盖了理论上无 需斜坡补偿的区间，最小化了斜坡补偿的需求（仅需坡度较小的补偿），保证了在此区间内 峰值电流控制的稳定。

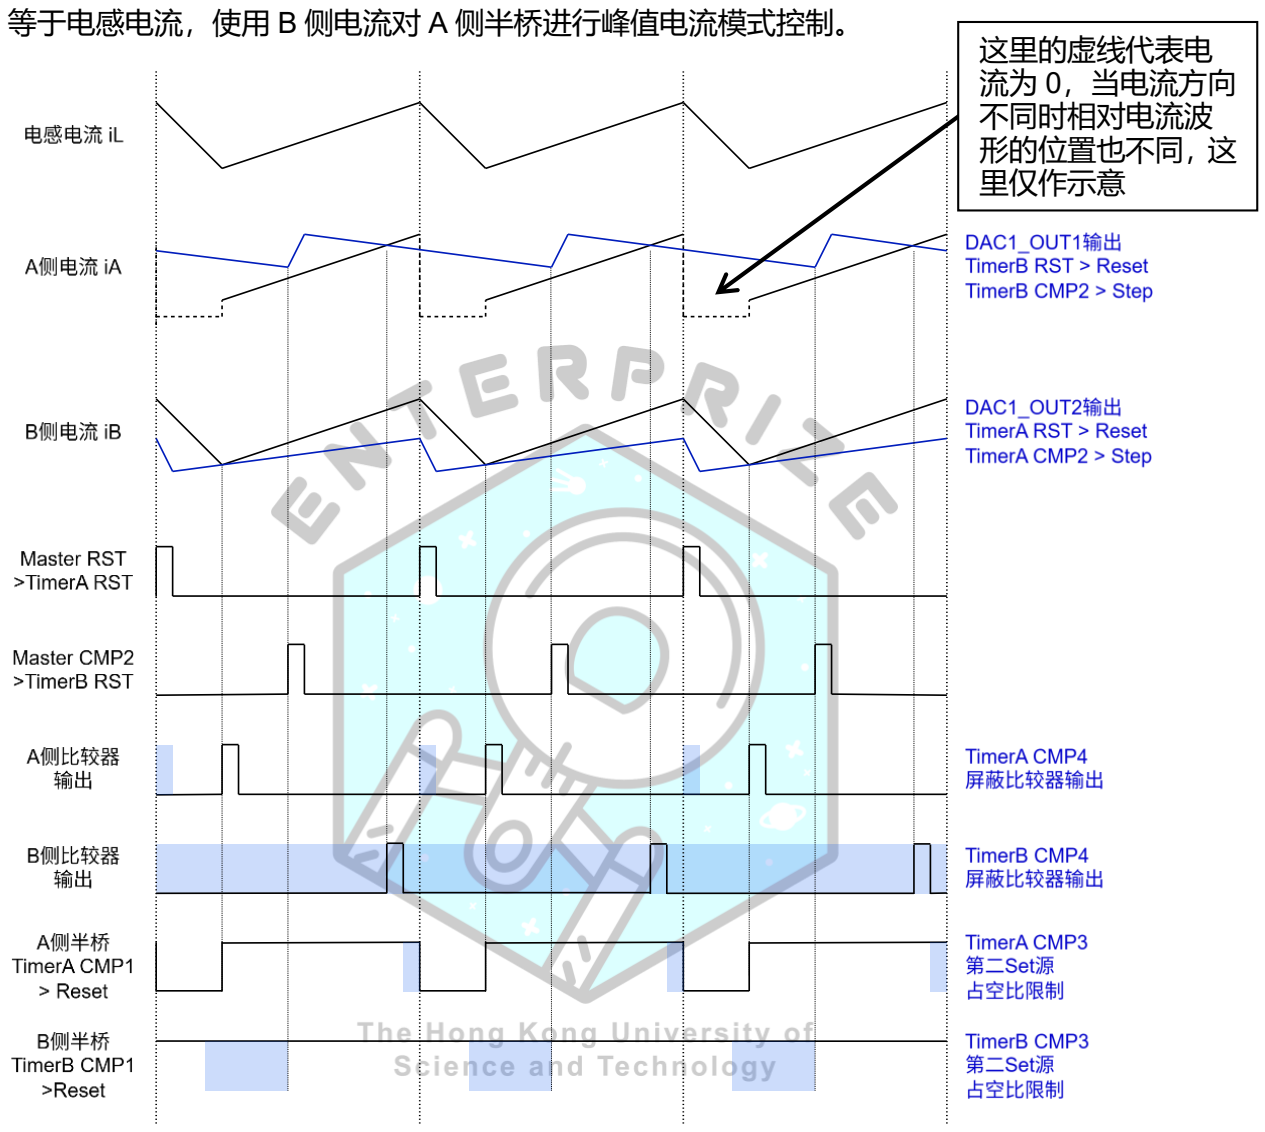
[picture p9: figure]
等于电感电流，使用 B 侧电流对 A 侧半桥进行峰值电流模式控制。; 这里的虚线代表电 流为 0，当电流方向 不同时相对电流波 形的位置也不同，这 里仅作示意

35 / 96

### 3.3.6 时序图

Buck 模式（iB 谷值电流）

Buck 模式下，A 侧半桥以 250kHz 频率开关，B 侧上管常开，此时 B 侧高位采样电阻电流

如图所示，因为 Buck 模式下只用到了 B 侧电流控制 A 侧半桥，所以对 A 侧电流对应的 B 侧比较器的输出进行屏蔽；同时将第二 Set 源（上一节中的 S1）触发时间设置为 0，以实 现 B 侧半桥上管常开。具体运行过程分为两阶段：

1. Master 复位事件同时触发 TimerA 的复位事件，TimerA CMP1（=0）触发 A 侧半桥和 DAC Reset，电感电流开始下降，电流斜率绝对值为 Vout⁄L
2. 电流下降到比较器阈值触发 A 侧比较器，进而触发 A 侧半桥 Set；如果比较器触发过晚 （超过 99%周期），则会由 TimerA CMP3 触发 Set，防止占空比过小。触发后电感电 流开始上升，电流斜率绝对值为 (Vin − Vout)⁄L

36 / 96

Buck-Boost (Vin > Vout) 模式（iB 谷值电流）

Buck-Boost (Vin > Vout) 模式下，AB 侧半桥都以 250kHz 频率开关，且周期相位相错 180°， 当 B 侧上管打开时，B 侧高位采样电阻电流等于电感电流，使用 B 侧电流对 A 侧半桥进行

如图所示，Buck-Boost (Vin > Vout) 模式下将 B 侧半桥设置为固定占空比，A 侧半桥使用 B 侧电流进行控制。通过屏蔽 B 侧比较器的输出，并把 TimerB CMP3 设置为在 16%周期时 触发以实现 B 侧 84%固定占空比输出。具体运行过程分为四阶段：

1. Master 复位事件同时触发 TimerA 的复位事件，TimerA CMP1（=0）触发 A 侧半桥和 DAC Reset，电感电流开始下降，电流斜率绝对值为 Vout⁄L
2. 电流下降到比较器阈值触发 A 侧比较器，进而触发 A 侧半桥 Set；触发后电感电流开始

上升，电流斜率绝对值为 (Vin − Vout)⁄L

3. Master CMP2 在半周期处触发 TimerB 复位事件，，进而触发 B 侧半桥 Reset，电感电 流开始上升，电流斜率绝对值为 Vin⁄L
4. TimerB CMP3 触发 B 侧半桥 Set，电感电流上升，电流斜率绝对值为 (Vin − Vout)⁄L

37 / 96

Buck-Boost (Vin < Vout) 模式（iA 峰值电流）

Buck-Boost (Vin < Vout) 模式下，AB 侧半桥都以 250kHz 频率开关，且周期相位相错 180°， 当 A 侧上管打开时，A 侧高位采样电阻电流等于电感电流，使用 A 侧电流对 B 侧半桥进行

如图所示，Buck-Boost (Vin < Vout) 模式下将 A 侧半桥设置为固定占空比，B 侧半桥使用 A 侧电流进行控制。通过屏蔽 A 侧比较器的输出，并把 TimerA CMP3 设置为在 16%周期时 触发以实现 A 侧 84%固定占空比输出。具体运行过程分为四阶段：

1. Master 复位事件同时触发 TimerA 的复位事件，TimerA CMP1（=0）触发 A 侧半桥和 Reset，电感电流开始下降，电流斜率绝对值为 Vout⁄L
2. TimerA CMP3 触发 A 侧半桥 Set，电感电流下降，电流斜率绝对值为 (Vout − Vin)⁄L
3. Master CMP2 在半周期处触发 TimerB 复位事件，，进而触发 B 侧半桥和 DAC Reset， 电感电流开始上升，电流斜率绝对值为 Vin⁄L
4. 电流上升到比较器阈值触发 B 侧比较器，进而触发 B 侧半桥 Set；触发后电感电流开始

下降，电流斜率绝对值为 (Vout − Vin)⁄L

38 / 96

Boost 模式（iA 峰值电流）

Boost 模式下，V 侧半桥以 250kHz 频率开关，A 侧上管常开，此时 A 侧高位采样电阻电流 等于电感电流，使用 A 侧电流对 B 侧半桥进行峰值电流模式控制。

如图所示，因为 Buck 模式下只用到了 B 侧电流控制 A 侧半桥，所以对 A 侧电流对应的 B 侧比较器的输出进行屏蔽；同时将第二 Set 源（上一节中的 S1）触发时间设置为 0，以实 现 B 侧半桥上管常开。具体运行过程分为两阶段：

1. Master CMP2 在半周期触发 TimerB 的复位事件，TimerB CMP1（=0）触发 B 侧半桥 和 DAC Reset，电感电流开始上升，电流斜率绝对值为 Vin⁄L
2. 电流上升到比较器阈值触发 B 侧比较器，进而触发 B 侧半桥 Set；如果比较器触发过晚

（超过 55%周期），则会由 TimerA CMP3 触发 Set，防止占空比过小导致 Boost 电压 过高。触发后电感电流开始下降，电流斜率绝对值为 (Vout − Vin)⁄L

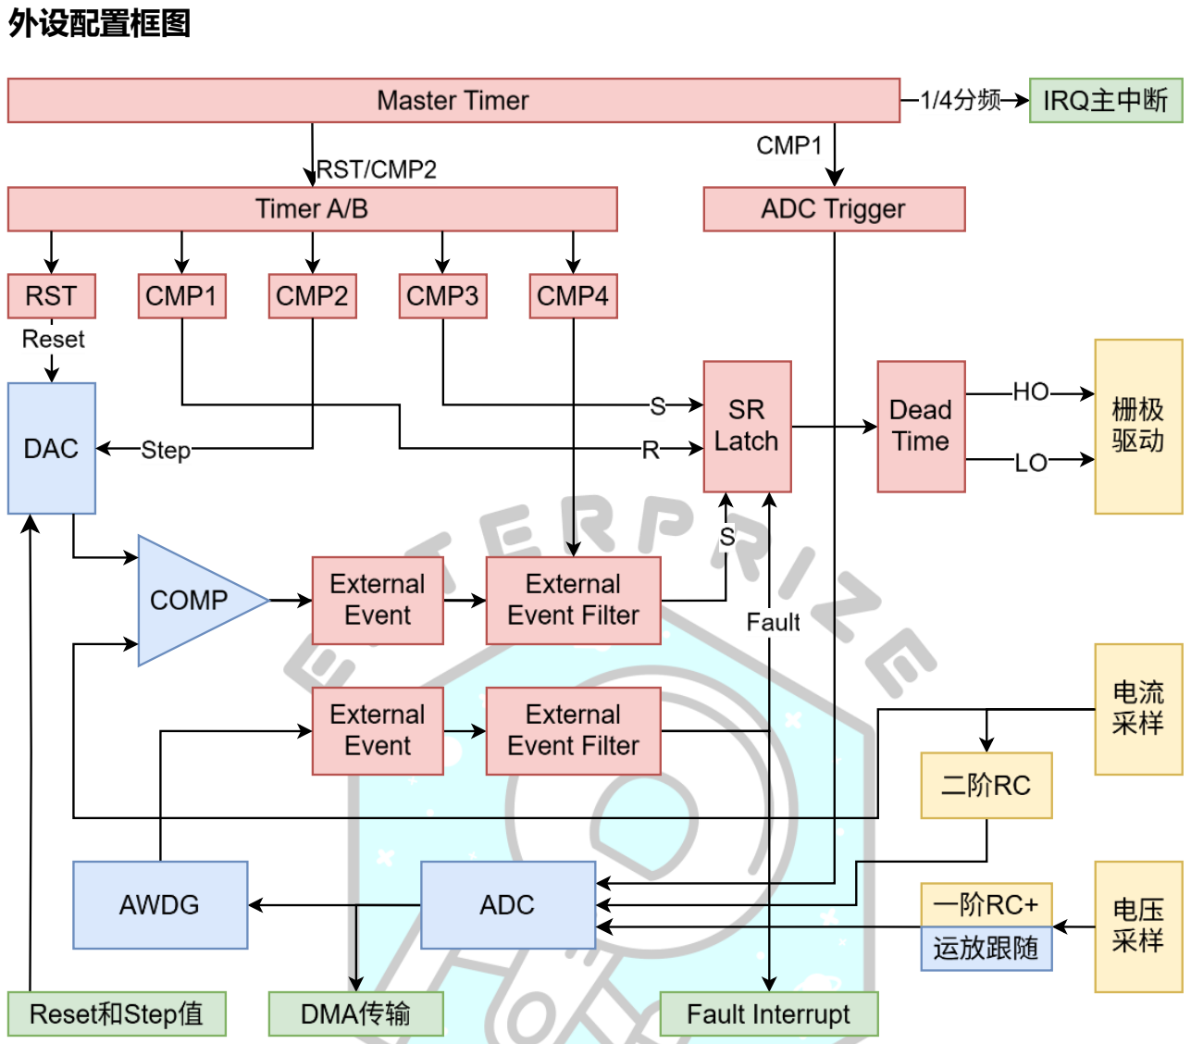
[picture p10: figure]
外设配置框图

39 / 96

### 3.3.7 MCU 外设配置

HRTIM 配置

STM32G474 的 HRTIM 可以提供 MCU 主频 32 倍的倍频速度，即 170MHz×32=5.44Ghz， 分辨率可达 184ps，非常有助于在固定占空比模式下输出精确的占空比。HRTIM 输出的本 质为一个多输入的 SR 锁存器，是实现峰值电流控制的关键。

为了使开关频率为 250kHz，将 Master Timer 和 Timer A、Timer B 的周期配置为 21760。

软件环路计算速度设定为 4 开关周期一次，所以将 Master Timer 的 Repetition Counter 配 置为 4-1，并启用全局中断，在代码中可以在对应的 IRQ_Handler 中执行环路计算和保护等 功能的代码。

40 / 96

为了实现 Buck Boost 两侧半桥交错输出，需要将 Timer A 和 Timer B 的相位相错。将 Timer

A 的复位源设置为 Master Timer 的复位事件，将 Timer B 的复位源设置为 Master Timer

CMP2，CMP2 的值设置为周期一半，这样就实现了两个子 Timer 的 180°交错输出。

虽然两个子 Timer 的相位不同，但为了保证其寄存器值更新的同步，将两个 Timer 的 Update 触发源都设置为 Master Timer 的复位事件。

CMP1 和 CMP3

CMP1 用于在每个周期开始时对 SR 锁存器进行 Reset，CMP3 则用于固定占空比或占空比

限制的 Set。

根据 AN4539 中对于不同比较单元优先级的描述，为了实现上管常开（即 100%占空比），

需要 Set 源的占空比比 Reset 源高，所以这里 CMP1 和 CMP3 间不能互换；因为 CMP1 和 CMP3 都可能出现值为 0 的情况，所以不能与 CMP2 或 4 互换（后者最小值为 96）。

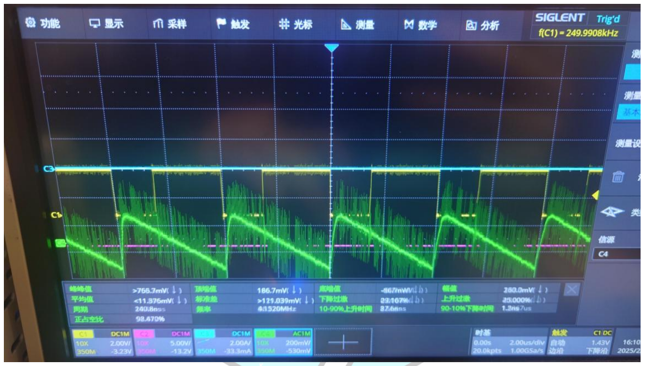
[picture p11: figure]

41 / 96

CMP2 和 CMP4

由于 DAC 在每个周期 Reset 后的上升需要一定时间，在这个过程中比较器可能意外触发， 所以使用对应子 Timer 的 CMP4 比较单元来屏蔽比较器的输入。

在上升后，使用 CMP2 来触发 DAC 开始输出三角波以进行斜坡补偿，CMP3 的值一直恒定 为周期的 5%。

在峰值电流控制下，通过测试 DAC 输出的上升时间，选择 CMP4 的值为周期的 6%。因为 模式切换会在 94%占空比前进入其他模式，所以实际此值可以取更大。如下图中绿色波形 曲线为 DAC 输出，黄色为 MCU 输出的半桥控制信号：

在固定占空比或上管常开模式下，需要完全屏蔽比较器的输入，所以对应地，需要将 CMP4 设置为占空比值或与周期相等的值。

ADC 采样时间

由于加入无线充电系统后，要采样的量更多，使得采样时间较为紧张，因为 ADC 引脚都有 小电容或运放跟随，所以采样时间可以较短。计算如下

根据 STM32G474RB 的数据手册，在 MCU 主频为 170MHz 时，ADC 时钟最快为 42.5Mhz

（4 分频）。

由于每个开关周期需要将所有量采样一次（超级电容系统 5+无线充电系统 2），使用 ADC1 和 2 一起采样，单个周期至少需要有进行 4 次采样的时间。

每个开关周期内 ADC 时钟的周期共有 42.5MHz⁄250kHz = 170cycle，每次采样时间为“采

样时间+12.5cycle”，所以将 ADC 采样时间配置为 12.5Cycle，总时间占用开关周期的 58.8%

42 / 96

ADC Trigger 配置

由于电压和电流采样在进入 ADC 前都有进行 RC 低通滤波，且截止频率都为开关频率的 1/10 左右，对于开关频率的信号（例如滤波前信号电感电流波形，滤波进入 ADC 后为每侧 平均电流）分别有-20dB（电压）和-40dB（电流）的衰减，所以对于采样时机要求不是很 严格，仅需在周期开始后一段时间内触发采样，计算如下：

测试说明，电流采样比电压采样更容易受到开关噪声的干扰，故将 iA，iB 两个电流采样设

定为 ADC1 和 2 的第一个采样 Rank。

为了最小化噪声，电流采样应在两次开关间，即周期的 1/4 或 3/4 处采样。考虑到电流采样 二阶 RC 滤波的相位延迟为 180°，将采样时间设定在 1/4 周期处。

将采样时间的 12.5cycle 对齐 1/4 周期，需要提前 6.25cycle 开始触发采样。每个 cycle 对

应的 HRTIM counter 数为 21760⁄170 = 128，故须在 1/4 周期上在提前 128 × 6.25 = 800 进行采样。

综上所述，ADC Trigger（Master Timer CMP2）的值应为 21760⁄4 − 800 = 4640

双 ADC 配置

STM32G4 系列支持 ADC1 和 2 的双 ADC 同步采样来提升采样结果的同步（例如同时采样 电流和电压），但是本系统中使用双 ADC 的主要原因是因为其可以将两个 ADC 采样的数

据（各 12bit）存入一个 32 为寄存器中，由于计算 uint16 和 uint32 的开销相同，双 ADC 采样在进行结果的累加平均时可以将开销减半。（以每开关周期进行采样，四开关周期进行 一次平均计算为例，12bit 的 ADC 原始数据进行四次加和最大为 14bit，不会对高 16 位数 据造成干扰。）

由于双 ADC 要求两个 ADC 的 Rank 数和每个 Rank 的采样时间相同，故引入一个冗余量来

满足此要求，实际每个 ADC 配置四个 Rank，采样时间均为 12.5cycle。

43 / 96

仅在 ADC1 中启用 DMA，数据为 32bit（word），优先级为 Very High，模式为 Circular， 将两个 ADC 的数据合并传输至一个变量中。

使能DMA Continuous Requests，使得每次采样后都进行DMA 传输，并将 Overrun behavior

设置为 overwritten 保证采样数据一直在更新。

软件启动采样的代码为：

void initADC()
{
//校准 ADC，ADC1 和 ADC2 用于同步采样，ADC4 用于监测温度和辅助电源 HAL_ADCEx_Calibration_Start(&hadc1, ADC_SINGLE_ENDED); HAL_ADCEx_Calibration_Start(&hadc2, ADC_SINGLE_ENDED); HAL_ADCEx_Calibration_Start(&hadc4, ADC_SINGLE_ENDED);
HAL_Delay(50);
//双 ADC 同步采样
HAL_ADCEx_MultiModeStart_DMA(&hadc1, adcData.rawData12, 4 * HRTIM_INT_SCALER); HAL_ADC_Start(&hadc2);
}
DAC 配置

配置 DAC 时将其调为高频模式，根据 RM0440 中对与 HRTIM 到 DAC 互联矩阵的描述，

将两个 Trigger 分别配置为对应 Timer中 Dual DAC Trigger的RST和STEP信号源。Polarity 根据 AB 侧不同配置选择上升或下降。Reset 和 Step 两个数据由软件更新：

__attribute__((section(".code_in_ram"))) inline void setInductorCurrent()
{
HAL_DACEx_SawtoothWaveGenerate(&hdac1, DAC_CHANNEL_2, DAC_SAWTOOTH_POLARITY_INCREMENT, PEAKI_TO_DACVAL((psData.iLTarget - 1.25f)), 180); HAL_DACEx_SawtoothWaveGenerate(&hdac1, DAC_CHANNEL_1, DAC_SAWTOOTH_POLARITY_INCREMENT, PEAKI_TO_DACVAL(-(psData.iLTarget + 1.25f)), 180); }

44 / 96

COMP 和 OPAMP 配置

运放设定为跟跟随器模式，并使用 High speed 模式提升压摆率。

在运放的输出端对引脚进行复用，将相同引脚用于 ADC 采样。不使用内部通道直连的原因 是外边连接可以通过测试点测量电压波形，方便调试。

比较器启用外部输出方便调试，由于其他功能都在 HRTIM 外设中实现，所以其余设置不做

特殊配置。

45 / 96

比较器与比较器触发的半桥控制信号如下图所示（由于是测试版本有轻微震荡），其中紫色 波形为比较器输出，黄色为 MCU 输出的半桥控制信号，比较器触发半桥 Reset：

电流感应放大器输出的电感电流波形（INA240 输出）：

对于运放，在启用前调用校准函数，最终模拟外设（除 ADC 外）初始化代码如下：

void initAnalog()
{
HAL_OPAMP_SelfCalibrate(&hopamp1); // 采样电压跟随 HAL_OPAMP_SelfCalibrate(&hopamp2); // 采样电压跟随 HAL_OPAMP_SelfCalibrate(&hopamp3); // 采样电压跟随 HAL_OPAMP_SelfCalibrate(&hopamp4); // 参考电压跟随

46 / 96

HAL_Delay(50);

HAL_OPAMP_Start(&hopamp1); HAL_OPAMP_Start(&hopamp2); HAL_OPAMP_Start(&hopamp3); HAL_OPAMP_Start(&hopamp4); HAL_DAC_Start(&hdac1, DAC_CHANNEL_2); HAL_DAC_Start(&hdac1, DAC_CHANNEL_1); HAL_COMP_Start(&hcomp2);
HAL_COMP_Start(&hcomp3);
}

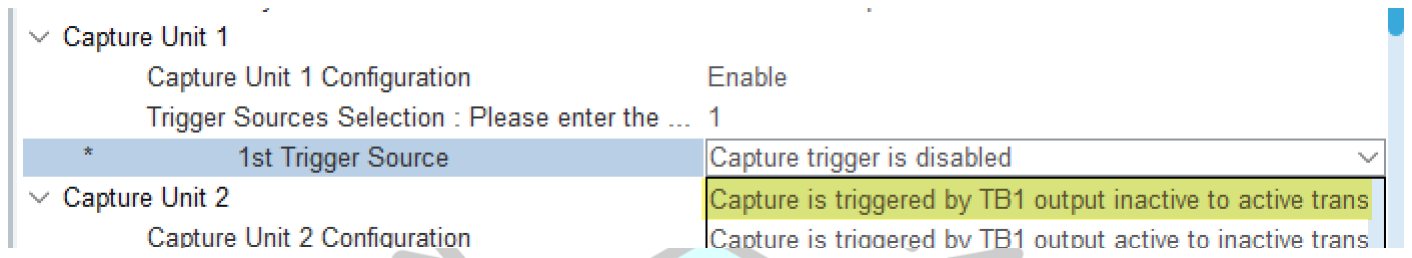
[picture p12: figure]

47 / 96

### 3.3.8 升降压模式切换

占空比测量

要进行状态切换首先要获知功率级的占空比。由于峰值电流模式控制的是电感电流的大小， 并不是直接作用于占空比，所以需要对占空比进行观察。

一种测量方式是使用HRTIM的Capture Unit获取半桥控制信号输出是Timer的Counter值， 通过 DMA 传入变量中，通过与周期值相除获取单边占空比，最终两侧占空比相除获取整体 占空比。但是此方法测量结果噪音较大，如果直接用于控制会引起不同运行模式之间的震荡。

所以在本系统中使用了另一种更为直接的方式，通过观测两侧电压 vA vB 并将其相除，获 取整体占空比。由于电压测量噪音极小，所以可以获得较为稳定的测量结果，并且仅需一次 除法即可完成计算。此方案缺点是由于 MOS 管、采样电阻的压降，占空比会有一定偏差， 但可以通过不同模式间留有余量的方式来保证模式间可以正常切换。

状态切换状态机

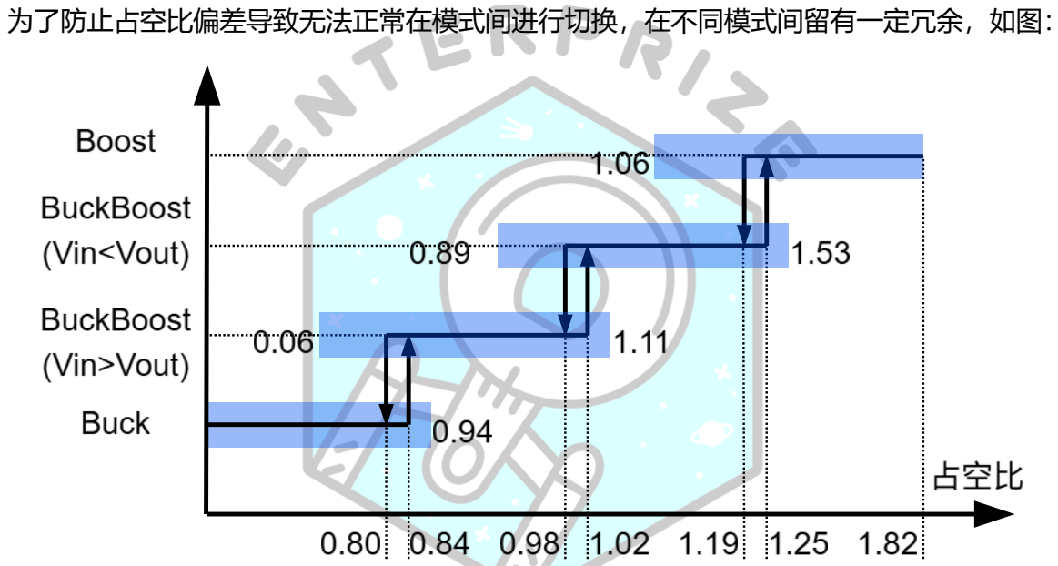
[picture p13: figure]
为了防止占空比偏差导致无法正常在模式间进行切换，在不同模式间留有一定冗余，如图：

48 / 96

如图即为不同模式间的状态切换方式。在开关频率 1/4 的中断中，处理完 ADC 后通过 D=vB/vA 的方式估算出占空比后，将 D 输入状态机进行不同模式的切换。

在不同模式间切换时，加入了施密特触发来防止在切换时震荡。例如 Buck 切换到 BuckBoost

(Vin>Vout) 时，占空比阈值为 0.84，而相反阈值则为 0.80。

对于除 Buck 以外的模式，都可以通过一定阈值直接切换回 Buck 模式，这样做的原因是加 快短路保护的响应速度。由于每 4 开关周期进行一次软件环路计算，例如限制功率级处于 Boost 模式，则至少需要 3 个软件周期或 12 个开关周期才能回到 Buck 模式，如果对每个 模式都设置直接切换至 Buck 模式的阈值，响应仅需 1 个软件周期或 4 个开关周期。这种做 法会提升不同模式下短路保护表现的一致性。

不同模式的运行范围

忽略上文提到的任意模式可直接切换至 Buck 模式的通路，图中蓝色部分为每个模式下允许 的最大和最小占空比，可以充分保证切换不会出现异常。例如 Buck 模式下占空比高于 0.84

就会切换到 BuckBoost，但实际 Buck 模式最高允许占空比为 0.94。

切换模式半桥输出

根据时序图和模式切换的需求，可见半桥输出效果需要达成三种模式：

- 周期开始 Reset，对侧峰值电流控制 Set，并且有最小占空比限制（Set）
- 固定占空比输出
- 常开

在占空比状态机后，根据现有模式进行相应的寄存器设定，具体代码如下：

__attribute__((section(".code_in_ram"))) void modeStateMachine()
{

49 / 96

//根据电压计算占空比
psData.dutyByVoltage = adcData.vB / adcData.vA;

//根据占空比进行状态切换
switch(psData.dcdcMode)
{
case BUCK:
if(psData.dutyByVoltage > 0.84f) psData.dcdcMode = BUCKBOOST; break;
case BUCKBOOST:
if(psData.dutyByVoltage < 0.80f) psData.dcdcMode = BUCK;
else if(psData.dutyByVoltage > 1.02f) psData.dcdcMode = BOOSTBUCK; break;
case BOOSTBUCK:
if(psData.dutyByVoltage < 0.82f) psData.dcdcMode = BUCK;
else if(psData.dutyByVoltage < 0.98f) psData.dcdcMode = BUCKBOOST; else if(psData.dutyByVoltage > 1.25f) psData.dcdcMode = BOOST;
break;
case BOOST:
if(psData.dutyByVoltage < 0.82f) psData.dcdcMode = BUCK;
else if(psData.dutyByVoltage < 1.19f) psData.dcdcMode = BOOSTBUCK; break;
default:
break;
}

//根据状态操作 HRTIM 寄存器，并分别计算 A 和 B 的占空比 switch(psData.dcdcMode)
{
case BUCK:
//A 侧限制 94%占空比
__HAL_HRTIM_SETCOMPARE(&hhrtim1, HRTIM_TIMERINDEX_TIMER_A, HRTIM_COMPAREUNIT_4, HRTIM_PERIOD * 0.06f); //A 侧限制 0.5%占空比
__HAL_HRTIM_SETCOMPARE(&hhrtim1, HRTIM_TIMERINDEX_TIMER_A, HRTIM_COMPAREUNIT_3, HRTIM_PERIOD * 0.995f); //B 侧常开
__HAL_HRTIM_SETCOMPARE(&hhrtim1, HRTIM_TIMERINDEX_TIMER_B, HRTIM_COMPAREUNIT_3, 0U);
//更新状态和 AB 占空比
psData.pcmMode = IB_VALLEY;
break;
case BUCKBOOST:
//A 侧限制 94%占空比

50 / 96

__HAL_HRTIM_SETCOMPARE(&hhrtim1, HRTIM_TIMERINDEX_TIMER_A, HRTIM_COMPAREUNIT_4, HRTIM_PERIOD * 0.06f); //A 侧限制 5%占空比
__HAL_HRTIM_SETCOMPARE(&hhrtim1, HRTIM_TIMERINDEX_TIMER_A, HRTIM_COMPAREUNIT_3, HRTIM_PERIOD * 0.95f); //B 侧固定 84%占空比
__HAL_HRTIM_SETCOMPARE(&hhrtim1, HRTIM_TIMERINDEX_TIMER_B, HRTIM_COMPAREUNIT_3, HRTIM_PERIOD * 0.16f); __HAL_HRTIM_SETCOMPARE(&hhrtim1, HRTIM_TIMERINDEX_TIMER_B, HRTIM_COMPAREUNIT_4, HRTIM_PERIOD * 0.24f); //更新状态和 AB 占空比
psData.pcmMode = IB_VALLEY;
break;
case BOOSTBUCK:
//A 侧固定 84%占空比
__HAL_HRTIM_SETCOMPARE(&hhrtim1, HRTIM_TIMERINDEX_TIMER_A, HRTIM_COMPAREUNIT_3, HRTIM_PERIOD * 0.16f); __HAL_HRTIM_SETCOMPARE(&hhrtim1, HRTIM_TIMERINDEX_TIMER_A, HRTIM_COMPAREUNIT_4, HRTIM_PERIOD * 0.24f); //B 侧限制 94%占空比
__HAL_HRTIM_SETCOMPARE(&hhrtim1, HRTIM_TIMERINDEX_TIMER_B, HRTIM_COMPAREUNIT_4, HRTIM_PERIOD * 0.06f); //B 侧限制 55%占空比
__HAL_HRTIM_SETCOMPARE(&hhrtim1, HRTIM_TIMERINDEX_TIMER_B, HRTIM_COMPAREUNIT_3, HRTIM_PERIOD * 0.45f); //更新状态和 AB 占空比
psData.pcmMode = IA_PEAK;
break;
case BOOST:
//A 侧常开
__HAL_HRTIM_SETCOMPARE(&hhrtim1, HRTIM_TIMERINDEX_TIMER_A, HRTIM_COMPAREUNIT_3, 0U);
//B 侧限制 94%占空比
__HAL_HRTIM_SETCOMPARE(&hhrtim1, HRTIM_TIMERINDEX_TIMER_B, HRTIM_COMPAREUNIT_4, HRTIM_PERIOD * 0.06f); //B 侧限制 55%占空比
__HAL_HRTIM_SETCOMPARE(&hhrtim1, HRTIM_TIMERINDEX_TIMER_B, HRTIM_COMPAREUNIT_3, HRTIM_PERIOD * 0.45f); //更新状态和 AB 占空比
psData.pcmMode = IA_PEAK;
break;
default:
break;
}
}

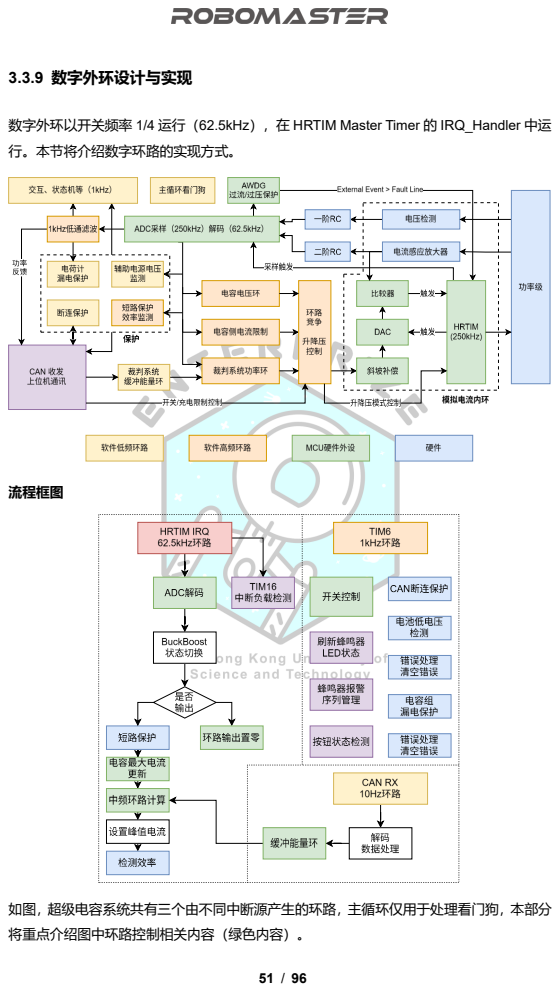
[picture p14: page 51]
3.3.9 数字外环设计与实现; 流程框图

数字外环以开关频率 1/4 运行（62.5kHz），在 HRTIM Master Timer 的 IRQ_Handler 中运
行。本节将介绍数字环路的实现方式。

如图，超级电容系统共有三个由不同中断源产生的环路，主循环仅用于处理看门狗，本部分
将重点介绍图中环路控制相关内容（绿色内容）。

52 / 96

ADC 解码

上文提到双 ADC 采样数据（32 位）由 DMA 传输至 uint32_t 数组中，每周期 4 个采样×4 个周期，数组大小为 16。

采样顺序为：ADC1 | iA iR | vA vWPT(无线充电输入电压)
ADC2 | iB iB(占位) vB iWPT(无线充电电流)

首先对 4 个周期的数据进行累加，得到 sumData[4]，再分别根据校准的斜率和截距解码， 例如对于 iA 和 iB 的解码，数据分别存在一个 uint32 的高 16 位和低 16 位：

adcData.iA = (1-ADC_ISENSE_ALPHA) * adcData.iA +
ADC_ISENSE_ALPHA * ((uint16_t)adcData.sumData[0] * ADC_IA_K + ADC_IA_B); adcData.iB = (1-ADC_ISENSE_ALPHA) * adcData.iB +
ADC_ISENSE_ALPHA * (*(uint16_t *)((uint8_t *)&adcData.sumData[0] + 2) * ADC_IB_K + ADC_IB_B);
在解码同时，对电流量进行一阶软件滤波，电压量实测噪音很小故不进行额外滤波。

** 此处的滤波不建议省略，省略滤波会造成噪声过大影响 PID，使得阶跃响应减慢

在直接测量量解码后进行间接量的计算，例如底盘功率、裁判系统功率、电容组功率等

adcData.iChassis = adcData.iR - adcData.iA;
adcData.pReferee = adcData.vA * adcData.iR;
adcData.pChassis = adcData.vA * adcData.iChassis;
最终，对特定量进行截止频率约为 1kHz 的软件低通滤波以供给低频环路进行相关运算，防 止 1kHz 环路直接使用 62.5kHz 环路的数据造成额外的噪声。以底盘功率为例，电容控制器 需要以 1kHz 的频率向主控板反馈底盘功率，所以需要对 pChassis 进行低通滤波后使用

adcData.pChassislf = MF_TO_LF_ALPHA * adcData.pChassis +
(1-MF_TO_LF_ALPHA) * adcData.pChassislf;

电容内阻补偿

由于电容组内阻约为 100-300mΩ级别，在大电流放电时会产生明显的压降，意味着测量电 压小于电容组内的实际电压，会造成放电时电流限制过早等问题。

具体做法为根据电容组侧电流 iB 在测量的 vB 上增加偏置，这种简单的补偿方法实测有非 常好的效果，其实现仅需一行代码，其后 vCap 用于电容组相关计算，而 vB 继续用于功率 级本身相关的计算：

adcData.vCap = adcData.vB - adcData.iB * CAPARR_DCR;
具体的调试方法为：
- 将 CAPARR_DCR 设为 0，在调试软件中绘制 vCap 的曲线
- 对电容组进行反复正反充放电切换（例如+5A 到-10A），同时调整 CAPARR_DCR 的 值，直到近似消除切换处的电压突变。

53 / 96

如图，棕色曲线为补偿后的电容电压，蓝色曲线为电流，可见基本消除了电容电压的突变。

更新电容最大电流

电容组电压处于正常范围时，电容组电流限制为裁判系统 CM01 的 15A。

由于电容组低电压时放电功率极大受限，所以需要在低压时严格限制电容组电流。

以 29V 电容组为例，电容组电压 10V 时电容组能量为 11.8%，以理论最大放电功率为 160W 放电仅能维持 1 秒左右；5V 时电容组能量为 3%，几乎耗尽。所以将电容组低压限制设定 为 10V，放电截止电压设定为 5V。对充放电电流进行限制：

如图可见在充放电时对电流的限制并不对称，如低压时允许较低功率充电，但几乎不允许放 电。

中频环路 1 – 裁判系统功率环

裁判系统功率环的核心为增量式 PID，其输入为 “裁判系统目标功率/底盘电流” 与 “当前裁 判系统端电流”，输出为增量式的电感电流。

其中增量式 PID 的写法延续了队伍去年开源中的写法，即将 P 项分为 pOnMeasuerment 和 pOnTarget 两项，分别进行调整以实现目标突变情况下的快响应、低过冲。实际调整中 后者约为前者的 1/2。

中频环路 2 – 电容组电压环

电容电压环主要由一个增量式的 I 环实现（PD 等为 0），这样做的原因如下：

- 经过测试单 I 控制完全可以较好地限制电压

54 / 96

- 62.5kHz 环路需要尽可能减小运算量
- 在只有 I 的情况下，通过调整 kI 值，使得输出端悬空时输出电压刚好会有轻微震荡，而 当电容组接入时则不会震荡，这样可以通过轻微震荡的特征来判断电容组断连以进行保 护，具体保护将在下文中说明。

中频环路 3 – 电容组电流限制环

由于峰值电流模式不能精确控制平均电流，故不能使用数控方式中直接限制电流环的目标值 来实现限流。实测中使用电流纹波估算限流的方式并不能很好限制输出电流，故额外引入了 两个环路来限制电流输出。

电容组电流限制环主要由两个个增量式的 I 环实现（PD 等为 0），将正反电流分别做限制， 选择 I 环的具体原因与上文的前两条原因相同：

- 经过测试单 I 控制完全可以较好地限制电流
- 62.5kHz 环路需要尽可能减小运算量

推测单 I 环即可较好限制的原因推测如下：虽然 I 环会引入过冲，但此过冲其实是电感电流 峰值的过冲，由于实际观测量为输出电流（经过了约 500μF 的电容），过冲部分的电流带 来的额外电荷可能被滤波电容吸收，故在观测输出电流时过充较小。

中频环路 – 竞争与输出

在分别计算完上文提到的三个环路后，将结果进行相互比较，最终输出一个目标电流的插值，

流程如下：

- 首先将目标电流差值设置为裁判系统功率环的结果
- 将目标值与电容组电压环输出进行比较，如果后者输出较小则直接输出结果，跳过后续

环路

- 将目标值与电容组电流环结果进行比较，以输出电流限制环为下限，输入电流限制环为 上限，对目标值进行限制。
- 将目标值（电流目标增量）累加到限制的峰值电流目标上
- 对峰值电流目标的绝对值进行限制，限制为电感的饱和电流以下（饱和电流 30A 左右， 实际限制为 25A），或在缓启动时进行电流限制。

mfLoop.deltaIL = mfLoop.iRPID.getOutput();
if(mfLoop.dIL_VCap_Max < mfLoop.deltaIL)
{
mfLoop.deltaIL = mfLoop.dIL_VCap_Max; ctrlData.limitFactor = CAPARR_VOLTAGE_MAX; }
else if(mfLoop.dIL_IB_Positive < mfLoop.deltaIL) {
mfLoop.deltaIL = mfLoop.dIL_IB_Positive;

55 / 96

ctrlData.limitFactor = IB_POSITIVE;
}
else if(mfLoop.dIL_IB_Negative > mfLoop.deltaIL) {
mfLoop.deltaIL = mfLoop.dIL_IB_Negative; ctrlData.limitFactor = IB_NEGATIVE;
}
psData.iLTarget += mfLoop.deltaIL;
psData.iLTarget = M_CLAMP(psData.iLTarget, -psData.iLLimit, psData.iLLimit);
裁判系统缓冲能量环

由于电流采样、电压采样都有一定误差，且功率限制以电源管理模块测得为准，所以需要对 电容控制器的功率误差作时时校准以从裁判系统中获取最大能量。

由于从上赛季开始裁判系统串口移除了功率反馈，所以这里使用与队伍上赛季开源的电容控 制器相同的方法，通过裁判系统缓冲能量对功率进行时时校准。

缓冲能量反馈频率为 10Hz，经由主控板通过 CAN，与其他信息一同反馈给电容控制器。由 于数据源刷新率为 10Hz，缓冲能量环也在 10Hz 环路中运行。

缓冲能量环使用位置式 PID 实现，输入为当前缓冲能量，目标值设定为 57J，目标值选择主 要考虑了距离缓冲能量上限 60J，可以更快达成闭环，同时留有较多余量。将输出直接以偏 置的方式增加到原有的目标功率上输入裁判系统功率环。

** 由于 57J 阈值较为接近 60J，所以 PID 容易产生震荡的情况，不影响正常工作
** 如果上位机反馈结果与测量差距过大，功控板会限制调整幅度（15W），如：上位机发 送功率限制为 50W，但反馈缓冲能量一直为 0J，功控板最低只会尝试闭环 35W。

开关控制与缓启动

裁判系统底盘断电时，电容不能向底盘继续供电，故需要对开关进行控制。开关控制状态机 在 1kHz 环路中运行，其以底盘电压为控制量进行施密特触发。

当功率级断电时，控制器依然由裁判系统功率环控制，由于此时裁判系统不会提供能量，地 盘电压会急剧降低，使用此特性来实现开关控制，逻辑如下：

- 当功率级断电时，如果底盘电压大于 20V，且没有进入错误保护，功率级则会启动
- 当功率级启动时，如果底盘电压小于 18V 时，功率级会关闭

为了防止上电瞬间的电流尖峰过大，当启动时，会限制裁判系统环的目标功率。

** 如果是轮腿机器人，建议将下电阈值调整至 15V，防止电池电压突降误触发关断 ** 由于过压保护阈值距离正常工作电压范围过近，所以当电压稍大于闭环值时会通过限制 占空比强制限制电压，防止过冲导致误触发过压保护

DAC 输出

当通过中频环路计算出得出电感电流目标后，需要通过 DAC 输出来将其转换为峰值电流内

56 / 96

环的输入。

峰值电流内环控制的是功率级的峰值电流，但是当在 BuckBoost (Vin<Vout) 与 BuckBoost (Vin>Vout) 模式切换时，峰值电流控制源会在 iA 峰值与 iB 谷值间切换，虽然配合外环闭环 速度很快，但还是不可避免地在切换模式引入电流波动。

由于不切换峰值/谷值控制时峰值电流的偏差并不重要（实测输出电压很低时为 1.4A 左右，

完全可由外环补偿），所以仅需在 BuckBoost (Vin<Vout) 与 BuckBoost (Vin>Vout) 模式切 换时对峰峰值电流做补偿。计算如下：

当模式切换时，输入输出电压几乎相等，都约等于 24V 左右，此时一侧为固定占空比 84%，另一侧占空比也约为 84%。

此时电感的电流纹波约为： ²⁴V
10uH

× (16% ×

1
250kHz) = 1.54A

在得到电流目标后，将其分别进行正反纹波 1/2 的偏置，并通过换算得到最终的 DAC 输出 值。由于 DAC 误差、斜坡补偿等原因，目标电流值仍有不可消除的偏差，但偏差值较小， 完全可以由外环进行补偿（峰值电流环绝对准度相对不重要）。

#define PEAKI_TO_DACVAL(x) ((x) * (HW_RSENSE * HW_IAMP_GAIN * 4096.0f / ADC_VREF) + 2048U)

HAL_DACEx_SawtoothWaveGenerate(&hdac1, DAC_CHANNEL_2, DAC_SAWTOOTH_POLARITY_INCREMENT,
PEAKI_TO_DACVAL((psData.iLTarget - HALF_IPP)), 180); HAL_DACEx_SawtoothWaveGenerate(&hdac1, DAC_CHANNEL_1, DAC_SAWTOOTH_POLARITY_INCREMENT, PEAKI_TO_DACVAL(-(psData.iLTarget + HALF_IPP)), 180);
响应速度

在实现峰值电流内环+数字外环后，电流响应速度极快，在 PID 参数留有一定余量的情况下， 外部电流的响应（经过 500uF 左右的滤波电容）可达 20μs 级别。测试中使用电流探头测 量外部电路，每 50ms 改变一次目标值，阶跃 1.5A 左右，结果如下图：

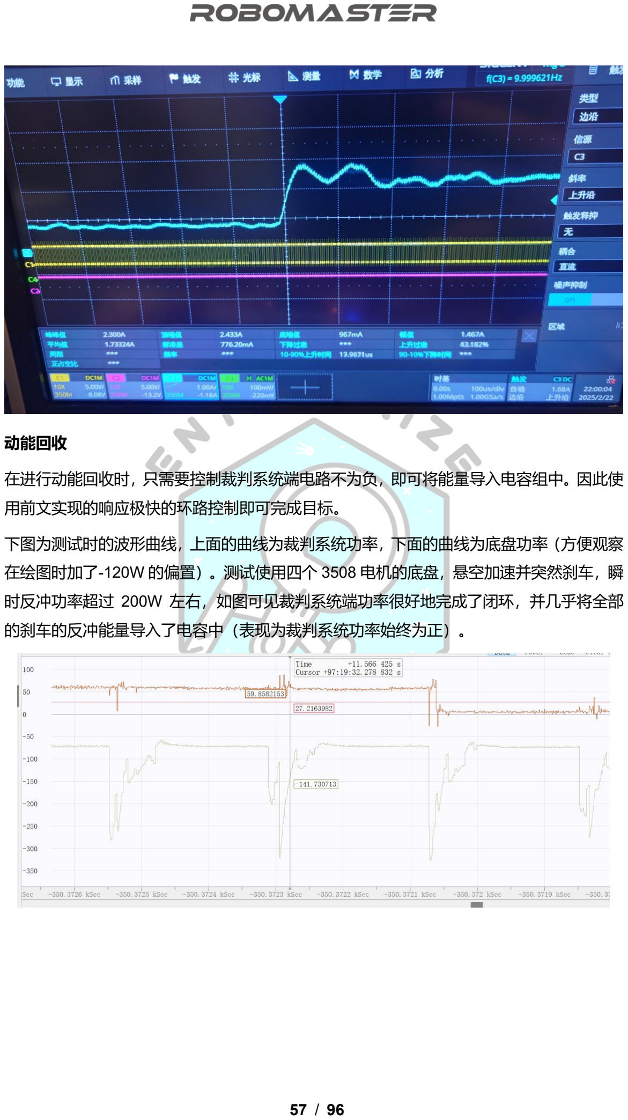
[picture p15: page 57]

57 / 96

动能回收

在进行动能回收时，只需要控制裁判系统端电路不为负，即可将能量导入电容组中。因此使 用前文实现的响应极快的环路控制即可完成目标。

下图为测试时的波形曲线，上面的曲线为裁判系统功率，下面的曲线为底盘功率（方便观察 在绘图时加了-120W 的偏置）。测试使用四个 3508 电机的底盘，悬空加速并突然刹车，瞬 时反冲功率超过 200W 左右，如图可见裁判系统端功率很好地完成了闭环，并几乎将全部 的刹车的反冲能量导入了电容中（表现为裁判系统功率始终为正）。

58 / 96

### 3.3.10 充电限制和纯电容模式

引入充电限制的原因

结合文章开始提到的单局能量限制的应对方法，需要对电容控制策略做出改变，通过引入电 容充电限制，例如在电容组充电 90%后不再从裁判系统获取能量主动充电来实现如下效果：

- 剩余 10%能量留给动能回收，防止电容充满时动能回收能量倒灌入裁判系统造成浪费
- 减少首先充入电容，再从电容流入底盘的能量，这样可以减小功率变换带来的损耗
- 一定程度上可以延长电容组寿命

使用场景

充电限制模式在正常运行时启动，但是当机器人即将投入战斗中或即将飞坡（需要较高爆发 能量），充电限制模式将关闭以最大化存储的能量。

具体实现方式

充电限制功能由主控板控制，主控板将通过开关 bit 和一个 uint8 格式的阈值来分别控制此 功能的开关和阈值。当受到开启信号后，将容量百分比阈值通过电容能量 E =

1
2

× C × U

2 的

关系映射到电容电压，作为控制的输入量。

在中频环路中通过阈值电压的施密特触发来改变裁判系统功率环的目标值，逻辑如下：

- 当电压上升到阈值电压+0.1V 时，将裁判系统目标功率设置为 6W（大约为电容控制器+ 底盘的静态功耗，此值设置太小会导致有能量倒灌入裁判系统造成浪费）
- 当电压下降到阈值电压-0.1V 时，将恢复裁判系统正常的功率目标值，即功率限制+裁判 系统能量环的校准偏置值

纯电容模式

由于无线充电系统的引入，在充电前电容组内需要有较多的空余能量以供接收电能。具体做 法是通过修改裁判系统的目标功率为很低的值，使得底盘优先从电容中获取能量，直到消耗 完大部分能量后转入裁判系统供电。此模式由操作手主动触发（例如返回补给区时将电容放 空以供无线充电）。

** 在进行无线充电时，需要保持纯电容模式且阈值电压最低，否则可能会出现从裁判系统 端取电为电容充电的情况

59 / 96

### 3.4 保护

由于超级电容系统涉及大功率的电压/电流变化，且电容组在满电时存储 2000J 的能量，如 果出现故障风险极大。所以在超级电容系统中需要完善的保护系统。

### 3.4.1 过压与过流保护

为了减小软件计算开销，并且提升保护响应速度，过压与过流保护使用模拟看门狗 AWDG 实现。这种方式在硬件上对 ADC 采样结果进行比较，如果超出阈值可触发特定事件的信号。

如上文所示的框图中所示，AWDG 信号接入 HRTIM 的 External Event，在通过过滤（事件 连续发生超过几次）后直接关断功率级，同时触发软件中断以进行相应处理。

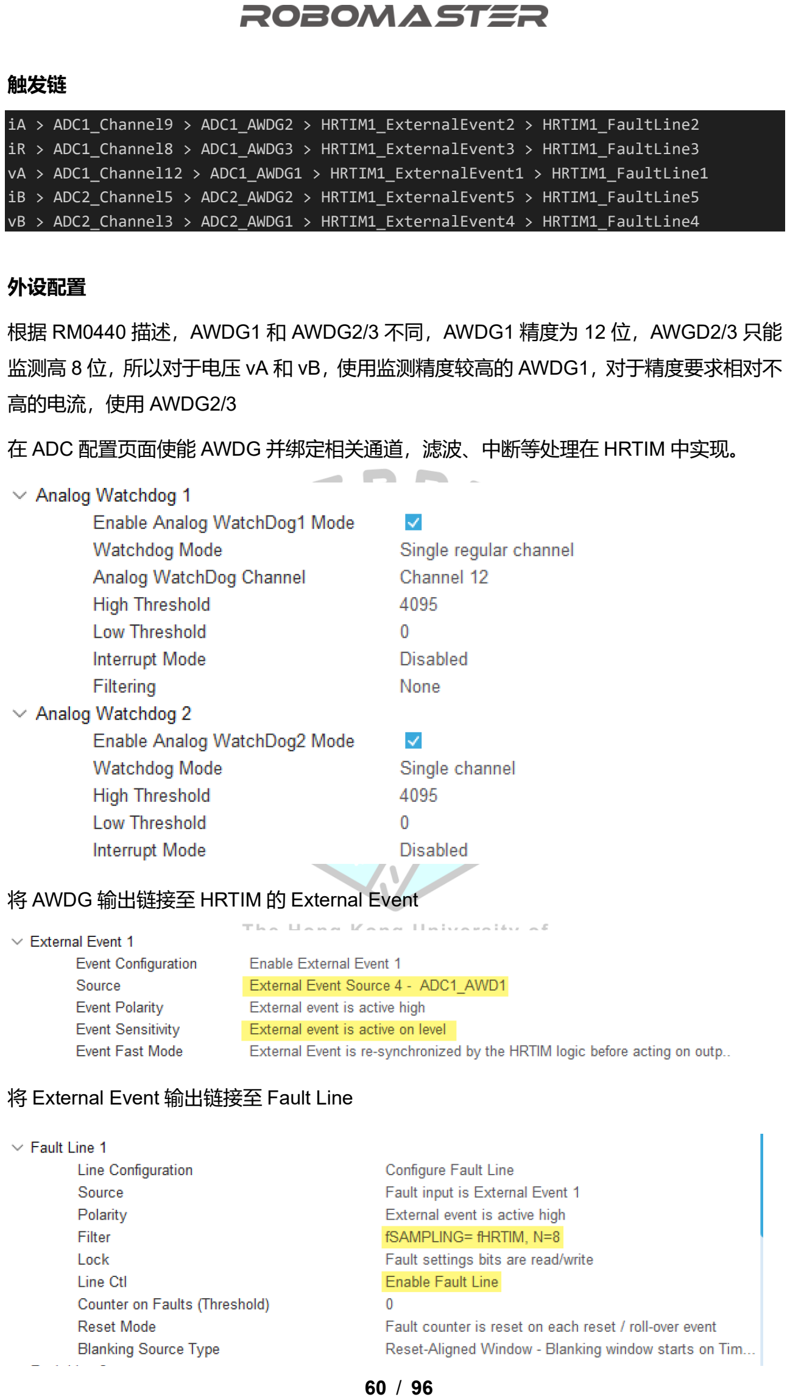
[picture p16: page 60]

60 / 96

触发链

iA > ADC1_Channel9 > ADC1_AWDG2 > HRTIM1_ExternalEvent2 > HRTIM1_FaultLine2 iR > ADC1_Channel8 > ADC1_AWDG3 > HRTIM1_ExternalEvent3 > HRTIM1_FaultLine3 vA > ADC1_Channel12 > ADC1_AWDG1 > HRTIM1_ExternalEvent1 > HRTIM1_FaultLine1 iB > ADC2_Channel5 > ADC2_AWDG2 > HRTIM1_ExternalEvent5 > HRTIM1_FaultLine5 vB > ADC2_Channel3 > ADC2_AWDG1 > HRTIM1_ExternalEvent4 > HRTIM1_FaultLine4

外设配置

根据 RM0440 描述，AWDG1 和 AWDG2/3 不同，AWDG1 精度为 12 位，AWGD2/3 只能 监测高 8 位，所以对于电压 vA 和 vB，使用监测精度较高的 AWDG1，对于精度要求相对不

高的电流，使用 AWDG2/3

在 ADC 配置页面使能 AWDG 并绑定相关通道，滤波、中断等处理在 HRTIM 中实现。

将 AWDG 输出链接至 HRTIM 的 External Event

将 External Event 输出链接至 Fault Line

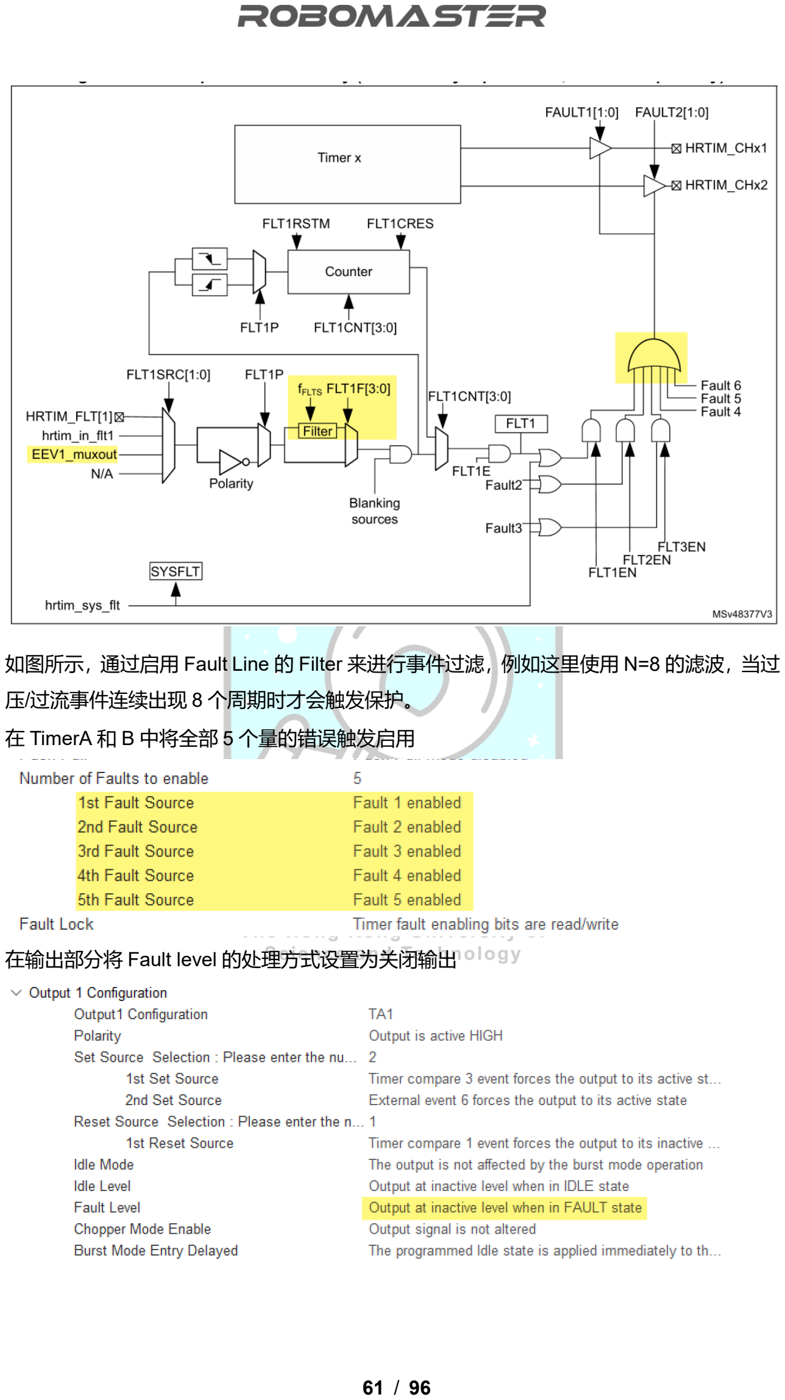
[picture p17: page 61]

61 / 96

如图所示，通过启用 Fault Line 的 Filter 来进行事件过滤，例如这里使用 N=8 的滤波，当过 压/过流事件连续出现 8 个周期时才会触发保护。

在 TimerA 和 B 中将全部 5 个量的错误触发启用

在输出部分将 Fault level 的处理方式设置为关闭输出

62 / 96

软件配置

根据 RM0440 描述，在启用 ADC 前配置 ADC1 和 2 的 TR1/2/3 寄存器来调整阈值，具体 代码如下所示，其中电压值上限按理论值计算，下限为 0，电流设置较为宽松设置为 27A

左右，计算方式为：Ilimit =

0xE0−2048U
4096U

× VRef ×

1
20V⁄V×2mΩ

void configAWDG()
{
ADC1->TR3 = 0x00E00020;
ADC1->TR2 = 0x00E00020;
ADC2->TR2 = 0x00E00020;
ADC1->TR1 = (uint32_t)(OVP_A/2.9f/16.0f*4095.0f) << 16; ADC2->TR1 = (uint32_t)(OVP_B/2.9f/16.0f*4095.0f) << 16; HRTIM1->sCommonRegs.IER |= 0b11111;
}
在配置完阈值后，通过 HRTIM 的 IER 寄存器启用全部五个中断源。

在软件的 IRQ_Handler 中进行软件上的错误处理，通过读取 HRTIM 的 ISR 获知错误源， 并进行错误状态更新，以 vA 过压保护为例：（此处关断输出的函数只是为了更新状态，实 际输出由硬件触发关断）

if(HRTIM1->sCommonRegs.ISR & HRTIM_FLAG_FLT1) //vA 过压保护触发
{
errorData.errorCode |= ERROR_OVP_A; errorData.errorLevel = ERROR_RECOVER_AUTO; HRTIM::disableOutputAB();
}

63 / 96

### 3.4.2 短路与功率级保护

短路保护

短路保护判定条件沿用了队伍上赛季开源的电容控制器的做法，通过电压小于一定阈值（如 5V）、电流大于一定阈值（如 5A）判断。由于涉及两个条件，且其中一个条件可能被经常 触发，故不适用 AWDG 和错误中断实现。

以 A 端短路保护代码为例，当两个阈值条件都满足时，开始进行错误计数器累加，同时更 新状态，当错误计数器累加带一定值后触发功率级关断，更新相关错误状态，并记录触发时 的电流和电压以供调试。

if(adcData.vA <= SCP_VOLTAGE && -adcData.iA >= SCP_CURRENT)
{
//裁判系统端或底盘端短路
errorData.errorLevel = WARNING; errorData.shortCircuitCnt +=600; if(errorData.shortCircuitCnt > 1100){ HRTIM::disableOutputAB();
errorData.errorCode |= ERROR_SCP_A; errorData.errorLevel = ERROR_RECOVER_MANUAL; errorData.errorVoltage = adcData.vA; errorData.errorCurrent = -adcData.iA;
}
}
例如上电时某瞬间 A 端过流条件被触发 1 次，此时计数器值为 600，后续无触发，那么计 数器会在低频环路中逐渐减小，当减为 0 时清除 WARNING 状态；但是如果短时间内触发 次数达到阈值，则会触发关断。

得益于峰值电流本身限制电流峰值的特性和较快的闭环速度，本设计的短路保护阈值较比数 控方案可以设置地很低。测试中 B 端电压在 29V 左右（电容组满电电压），将输出短路， 短路后保护瞬间触发，短路过程中无明显火花，且多次触发也不会损坏功率级。

效率监测

当 A 侧电流绝对值大于 0.5A 时，根据电流流向计算功率级转换效率，如果效率过低则进行 关断保护

辅助供电监测

由于本设计中电源网络较多，当 MCU 正常工作时只能说明 3.3V 网络供电正常，此时如果 3.3VA、10V 或 5V 网络故障会导致严重后果，本设计使用四个电阻（分别指向三个电源网 络和 GND）组成分压网络，当所有电源电压正常时，ADC 读取值应为 1.41V 左右。排除仅 使用烧录器供电的情况，当此电压不正常时可以通过禁止启用功率级输出来保护控制器。

64 / 96

### 3.4.3 通讯断连保护

当电容组至主控板的 CAN 信号断连时，需要进行错误处理来防止超功率等情况发生（例如 功率限制更新不及时等因素引起）。

软件设计上，在每次 CAN RX 中断中更新一个时间戳（方便调试），并更新连接状态，在 1kHz 的环路中将时间戳与当前时刻作比较，如果超过 500ms 即视为断连。

断连后将所有接收到的数据清空，并关闭所有特殊模式（纯电容模式和充电限制），将裁判 系统功率目标值设定为 37W（考虑到今年虚弱模式的加入，此阈值后续可能还需要调整）。

### 3.4.4 电容组漏电/断连保护

由于 RM 比赛中电容组一般为自行设计并手工焊接，有概率出现接触不良或漏电（如均衡 保护失效）等情况，此时需要电容控制器对其进行保护。原理主要根据公式：∆Q = C∆U

保护算法同时监测两个量，分别为电荷量与电压。具体实现如下：

- 在 1kHz 环路中积分电流获得电荷量（实测 62.5kHz 环路中积分噪声较大），在 62.5kHz 环路中监测电压的最大值和最小值。
- 如果电荷量达到一定阈值，与电压差值进行一次相除，为了防止电压不变而 0 为分母的 情况，实际上使用“电压差/电荷差”与容量阈值的倒数做对比。
- 如果电压差达到一定阈值，与电荷量进行一次相除，为了电荷量电压不变而 0 为分母的 情况，实际上使用“电荷差/电压差“与容量阈值做对比。
- 如果长时间二者都没有达到阈值，则清空两个量，重新开始积分。
- 根据触发情况累加错误计数器，当达到一定阈值认为电容组故障。

这种算法实测可以很好地处理电容组断连、漏电等情况。当等效容量过低则认为电容组断连， 容量过高认为电容组漏电。

断连测试

前文提到电容组不连接时 vB 的电压环被有意调整为轻微震荡，此时电压差会很快达到阈值， 由于未连接电容，电荷量积分几乎为 0，可以触发保护。

漏电测试

将电容组输出并联到电子负载，以恒流模式放电，实测当放电电流 1A 左右时开始触发保护。

实际使用中错误保护触发不会直接关断输出，而是会通过蜂鸣器提醒用户，如果频繁触发则 说明需要检查接线或更换电容组。

** 电量耗尽后首次充满可能会触发一次漏电提示音（电容单体误差导致），属于正常现象

65 / 96

### 3.4.5 错误分级处理与其他保护

错误分级

为了更好地处理错误，本设计将错误分级，并且为每个错误都分配对应的 errorCode：

enum ErrorLevel
{
NO_ERROR = 0, | // 无错误
ERROR_RECOVER_AUTO = 1, | // 错误，可通过自动恢复
ERROR_RECOVER_MANUAL = 2, | // 错误，可通过发信息恢复
ERROR_UNRECOVERABLE = 3, | // 错误，不可恢复
WARNING | // 警告
};

当 WARING 等级错误触发时（一般为短路保护的条件达成但未达到触发阈值），1kHz 环 路中会进行错误计数器的减小。

当 ERROR_RECOVER_AUTO（过流或过压）触发后，会在 5s 后尝试重启进行恢复。

当 ERROR_RECOVER_MANUAL（短路保护）触发后，将不会自动恢复，可以通过 CAN 向电容发起错误清除命令或通过按钮手动清除。

当 ERROR_UNRECOVERABLE（功率级错误）触发后，不会自动恢复，需要拆掉控制器 进行错误排查。

UID 检测

由于不同控制器的校准参数不同，在初始化中会读取 STM32 中的 96 为 UID 并进行对比， 如果与校准数据中不相符则停止初始化并报警。

** 可以通过启用 CALIBRATION_MODE 绕过此保护

过温检测

硬件上使用 NTC 电阻进行过温检测，实际使用中发现电容控制器发热并不严重，故此故障 保护暂时没有启用，仅作硬件预留。

** 测试发现由于布局问题，外置 NTC 的读数会受功率级开关影响，建议使用 MCU 内置的 温度传感器，可一定程度上监测过热的情况

66 / 96

## 3.5 通讯与交互

### 3.5.1 CAN 通讯

超级电容控制器与主控板通讯主要通过 CAN 进行，数据格式大致与队伍上赛季的开源相同， 并作出一定调整。例如将错误码改为状态码，反馈更多信息，并加入裁判系统功率反馈。

反馈信息（电容>主控板）

在 1kHz 环路中会将电容电量、状态信息、底盘功率、裁判系统功率、最大可输出功率等信 息进行打包，并以 1kHz 的速度反馈给主控板

static void generateTxDataNew(TxDataNew &td)
{
td = {};
td.statusCode = 0x00;
td.statusCode = (psData.outputABEnabled << 7) | (ctrlData.refLoop.useNewFeedbackMessage << 6) |
(ctrlData.wptStatus << 4) |
(((ctrlData.limitFactor >= 4) ? 0b11 : (ctrlData.limitFactor & 0x03)) << 2 ) |
(errorData.errorLevel & 0x03);
td.capEnergy = (adcData.vCaplf*adcData.vCaplf * (1/(CAPARR_MAX_VOLTAGE*CAPARR_MAX_VOLTAGE))) * 250U;
#ifdef WPT_HARDWARE

if(psData.outputEEnabled)
td.chassisPower = (adcData.pChassislf - adcData.pWPTlf) * 64U + 16384U; else
td.chassisPower = adcData.pChassislf * 64U + 16384U;
#else

td.chassisPower = adcData.pChassislf * 64U + 16384U;
#endif

td.refereePower = adcData.pRefereelf * 64U + 16384U;
td.chassisPowerLimit = CAPARR::getMaxPowerFeedback() + rxData1.refereePowerLimit; }

考虑到上位机需要得知无线充电功率来进行能量相关计算，所以在无线充电启用时将其累加 在底盘功率上（性质相同）。

信息包长度为 8Byte，并根据新老数据格式不同向不同 CAN 地址发送信息以作区分。

struct TxDataNew { | // 0x052 (useNewFeedbackMessage = 1)
uint8_t statusCode; | // 状态信息
uint16_t chassisPower; | // 底盘功率，功率*64+16384 (-256W~+768W, 精度 0.015625)
uint16_t refereePower; | // 裁判系统功率，功率*64+16384 (-256W~+768W, 精度 0.015625)
uint16_t chassisPowerLimit; | // 底盘最大可用功率（包括裁判系统）
uint8_t capEnergy; | // 电容现有能量，0-255
} __attribute__((packed));

67 / 96

接收信息（主控板>电容）

主控板以 10Hz 频率向电容发出指令，格式为：

struct RxData {
uint8_t enableDCDC: 1; | // 允许启动 DCDC
uint8_t systemRestart: 1; | // 系统重启
uint8_t resv0: 3;
uint8_t clearError: 1; | // 手动清除可清除的错误
uint8_t enableActiveChargingLimit: 1; | // 是否启用主动充电限制
uint8_t useNewFeedbackMessage: 1; | // 是否使用新的反馈消息格式
uint16_t refereePowerLimit; | // 裁判限制功率，单位 W
uint16_t refereeEnergyBuffer; | // 裁判能量缓冲，单位 J
uint8_t activeChargingLimitRatio; | // 主动充电限制比例（能量），0-255
int16_t resv2;
} __attribute__((packed));
当收到命令后，进行解包并进行相应操作，例如当 systemRestart 为 1 时，会直接触发系统 的重启：

if(rd.systemRestart)
{
HRTIM::disableOutputAB();
__disable_irq();
while (true)
NVIC_SystemReset();
}

CAN 总线保护

STM32G4 系列的 CAN 总线在错误累计一定数量后会进入 Bus Off 状态并不会自动恢复， 所有在每次发送数据前通过读取 PSR 寄存器中的 BO 位来判断是否触发，如果触发则写入

CCCR 寄存器中的 INIT 位来恢复。

### 3.5.2 交互

按钮交互

电容控制器在硬件上留有一个按钮，允许在不连接调试线的情况下进行操作，设计上长按 3 秒以上会进行 NVIC_SystemReset 重启整个系统，长按 1 秒以上、2 秒以下则会清除

ERROR_RECOVER_MANUAL 级别的错误。

蜂鸣器与 LED

电容控制器内置蜂鸣器三个 WS2812 LED 进行状态反馈。

在系统启动和功率级开关时，蜂鸣器会通过不同声音来发出提示。

进入错误保护时，根据错误等级不同，通过不同数量的高音+低音组合来提升错误等级和错 误点。例如 B 侧短路保护报警音位 4 高+2 低。

68 / 96

## 3.6 超级电容组设计

### 3.6.1 需求分析

RoboMaster 规则限定超级电容组的要求如下

- 标称容量不得超过 2000J，实测容量不得超过 2200J
- 供电电压不能超过 30V

在实际设计过程中，对电容组还有其他要求

- 要有完善的保护外壳
- 体积尽可能小
- 实际容量尽可能大
- 放电功率尽可能大

### 3.6.2 电容选型

单体电压选择

现在可以购买到的超级电容单体电压一般有 2.5V、2.7V 和 3.0V 三种（锂离子电容由于功 率过小且不能完全放电不考虑在内）。由于本赛季队内对于机器人体积压缩要求很高，所以 优先选能量密度更高的 3.0V 电压单体。

单体组合方式

电容组总能量的及算法方式为

E =

1
2

×

C
b

× (bU)

2 < 2000J

其中 C 为单串容量，b 为串数，U 为单体电压。由于单体耐压越高，理论上最大放电功率 越大（放电电流被 CM01 限制在 16A），所以满电电压尽量接近 30V，所以这里选择 10 串 的配置来达到规则限定下的最大电压 30V。

根据公式反推，单体容量最大为 44.44F，在进行反复的配对组合尝试后，最终选择使用 3.0V 34F 的单体+10F 的单体来使得单串容量为 44F，此时 E = 1980J < 2000J，符合规则要求。

这种电容单体组合方式有 ETN TV 或 CDA 品牌可选，经测试发现 CDA 的电容单体容量表

现都更为优秀，所以选择 CDA 的 CXP-3R106R-TWQ 和 CXP-3R0346R-TW 两个型号。

根据数据手册计算，理论最大瞬时电流为 8.96 + 21.93 = 30.89A，整体内阻为 (68mΩ ∥

69 / 96

45mΩ) × 10 = 271mΩ，实测内阻约为 150mΩ 左右。总体性能可以满足要求。

### 3.6.3 原理图与 Layout

保护电路

均衡电路考虑电路精简性选用了 BW6103 芯片，为了实现更大放电功率使用了外置 MOS 管串联大功率电阻进行放电。

由于 BW6103 的警示灯在电容电压很高（3.25V）时才会亮起，所以在控制 MOS 的栅极上 也加入一个黄色 LED 来指示泄放状态，方便调试，BW6103 的输出引脚电流可达 200mA， 足够驱动一个额外的 LED。

当某些电容单体在满电被放电均衡，其中的电荷量会减少，这会导致在整个电容组放电至接 近 0V 时某些电容单体出现负压的情况，所以使用两个低 VF 的肖特基势垒二极管（图中

B16WS）进行保护。

外置 MOS 管选择耐压 20V 最大电流 65A 峰值 DFN3x3 的 AP2045Q，选择原因是其栅极 开启电压阈值较低，可以保证电容单体达到泄放电压时完全开启。

在整个电容组的输出放置一个 30A 的快断保险丝，放置电容组输出意外短路，此保险丝比 电容控制器的输出保险丝 20A 要大，原因是电容组保险丝熔断更加危险（由于内部依然带 电，保险丝熔断难以放电）。

泄放电阻选用两个 2512 封装 1.5Ω的厚膜电阻串联，最大放电电流约为 1A

PCB Layout

Layout 上主要考虑因素如下

- 主电流回路要尽可能粗，减小损耗
- 保护电路尽量对称排版，方便 Layout 和维修，并且降低焊接时焊错元件的风险
- 保护电路的功率回路尽量短

整体 Layout 如下：

70 / 96

如图，电容泄放电流的 Layout 基本对称，并保证了泄放回路较短，对大功率回路在背面进 行了开窗处理，正面全部为功率回路的覆铜。

电容组排布

电容组的排布如右图所示，34F 的单体并列排布，10F 的单体一侧与 34F 的单体交错排布， 另一侧在背面横向焊接，这样做可以最大程度地缩小体积。

这样的排布方式可以将电容组的体积完全控制在装甲板支架之内，相当于整车无需再底盘上 预留额外空间，大大减小了超级电容系统的体积占用。

71 / 96

### 3.6.4 保护外壳

由于电容组单体较为瘦高，电容组外壳需要提供完善的保护和支持。设计时上下两个外壳为 TPU 材质，完全贴合电容单体。加之电容组内部使用 UV 胶进行单体与 PCB 板之间的加固， 整个电容组的抗摔能力较强。

72 / 96

焊接好的实物图

安装效果展示（完全嵌入装甲板内）

** 焊接注意事项请参考电容组开源。

** 请勿长时间过压使用电容组，如发现均衡 LED 一直点亮建议立即放电进行排查，否则可 能有过热损坏风险

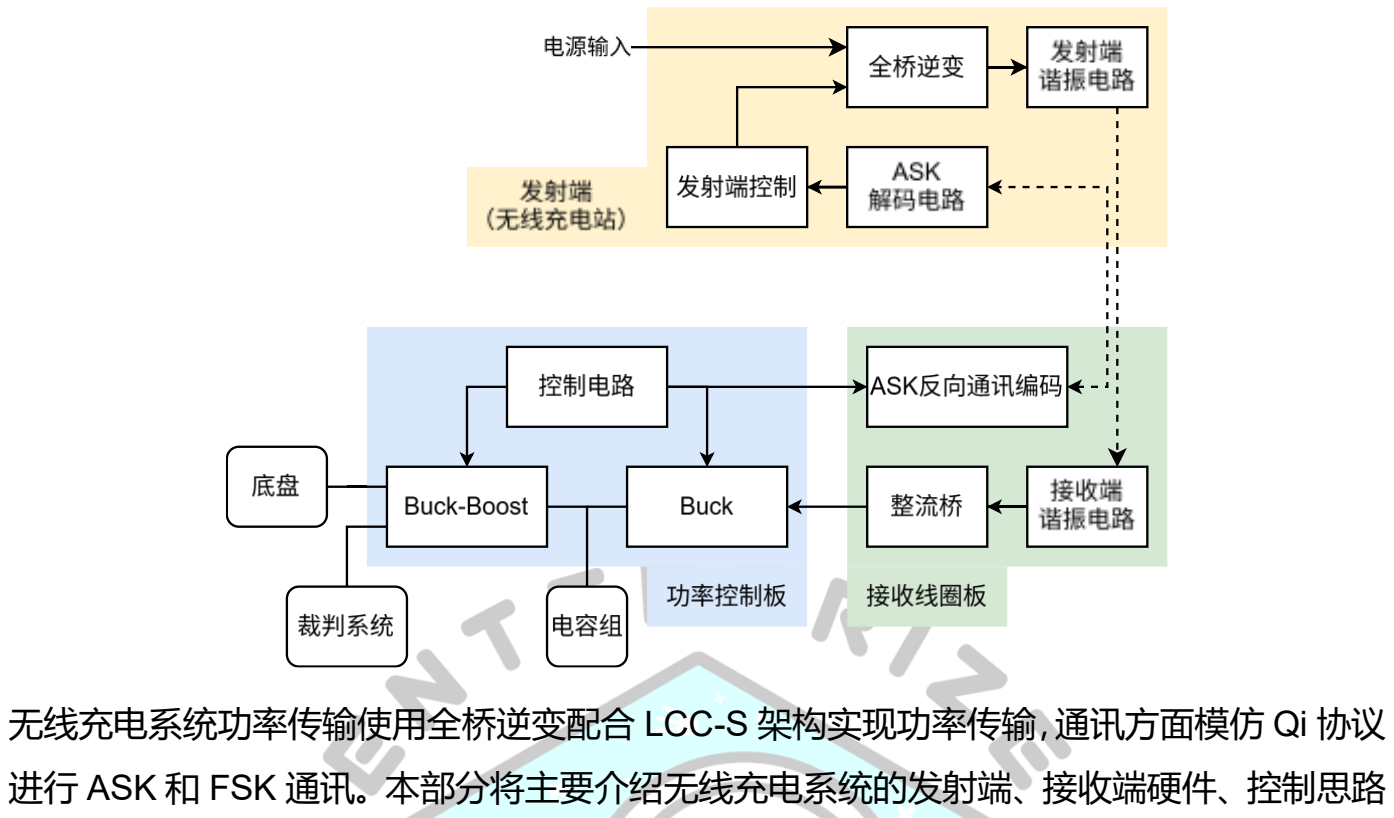
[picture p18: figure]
无线充电系统功率传输使用全桥逆变配合 LCC-S 架构实现功率传输，通讯方面模仿 Qi 协议; 进行 ASK 和 FSK 通讯。本部分将主要介绍无线充电系统的发射端、接收端硬件、控制思路

73 / 96

## 4. 无线充电系统

以及通讯的实现方式。

### 4.1 发射端

总体上，发射端控制板主要由功率级（逆变全桥）、谐振电路、采样与反馈电路、辅助供电、

ASK 解码几大部分组成。MCU 选用与功率控制板上相同的 STM32474RBT3，输入为 24V， 并预留有 24V 输出接口与 CAN 通讯电路（如果对位机构需要电机）。

为了加快设计与迭代，无线充电系统硬件方案很多与功率控制板相似，说明会较为简略。

74 / 96

### 4.1.1 功率级及驱动

全桥部分原理图

MOS 选型

全桥使用了四颗 BSC070N10 作为开关管，由于无线充电谐振频率不高（100-150kHz 级别）， 所以选型相对较为宽松。Vgs 10V 下 30nC 的栅极电荷量、6.0mΩ内阻、最大过流 80A、

VDS 耐压 100V 对于此应用完全足够。

滤波电容

滤波电容每侧采用三颗 50V 10μF 1206 的贴片电容滤除高频噪声，母线上采用两个 220μF 固态电容用来稳压和滤除低频干扰。

电流采样

电流采样选择在两个低位 MOS 的 S 极进行低位采样，阻值选择 2mΩ（与功控板一致）。

PCB 布局

PCB 布局上最小化了大功率回路的面积，供
电从背面通过固态电容的滤波进入高位
MOS，陶瓷电容紧贴半桥的两端。

75 / 96

### 4.1.2 谐振电路

原理图

发射端谐振电路为 LCC 拓扑，通过谐振电感和电容后输出连接到线圈。

PCB 布局

谐振电感选型

在第一版测试板中，发现谐振电感电流很大且发热较大，所在在这版中选用 90125 大小的 铁硅铝电感。

后来在与华南虎战队的交流中得知此处需要使用铁粉芯磁芯并配合 150 或 200 股利兹线制 作谐振电感，更换后效果极好，几乎没有发热的同时将传输效率提升至 85%-86%。

** 以 6μH 目标值时，建议预留 1m 以上的利兹线进行绕制

** 磁芯型号为：T141-2 羰基铁粉芯（外径 36*内径 11 厚度 11mm）

76 / 96

谐振电容选型

谐振电容预留了 CBB 电容与 1206 尺寸 COG（由于 X7R 和 X5R 容值会变所以只能使用 COG）电容的焊盘位。CBB 电容的优势是价格较低，且耐压很高，但缺点是受热时稳定性 较差，且过热严重会直接导致电容报废。而高耐压的 COG 电容价格较高，但性能更加优秀。

在测试后发现 CBB 电容发热比较严重，且出现过电容过热失效的情况，考虑到高耐压的 COG 电容用量很小，后续全部采用 COG 材质，耐压至少 100V 的谐振电容。

** 谐振电容尤其建议通过正规渠道购买，建议买后进行测试，防止耐压不足导致击穿

线圈选型

规则限制线圈能量交互面不得大于 10000 平方毫米，选择外径 80mm，内径 30mm，感值 为 14uH 的线圈，发射接收端对称。

实测加入隔磁片后自感值约为 20μH，通过正反串接的方法可测得线圈相距 2cm 时的互感。

** 本设计必须使用隔磁片，否则会导致工作异常，请避免在无隔磁片的情况下工作

谐振参数计算

为了满足理论无功为 0 的要求，需要满足如下关系：

ωLp =

1
ωCp

ωCs =

1

ω(LCoil − Lp)

为了尽量减小电感与电容的取值，将谐振频率最大化，取规则上限的 148.5kHz（实际后因 方便软件滤波算法改为 144kHz）

ω = 2πfs

在传输最大功率 120W 时，接收端电源需要可以达到 30V 作用。发射端通过移相全桥，等 效电压为 0V-24V，调整谐振电感值以获得足够的电压增益，理想情况下满载时全桥输出电 压为最大电压的 1/3-1/2 左右较合适；如增益不足可能导致接收端电压不足，充电功率受限， 此时需要减小谐振电感值。测试后最终目标取值为 6μH。

Gain ≈

M
Lp

谐振电感取 6μH 后，实际使用电桥测量感值在 100kHz 下为 5.77μH，根据以上关系可以计 算其他计算参数：

Cp = 199.07nF Cs = 80.72nF

接收端 S 电容参数为

ωLS =

1
ωCS

→ Cs = 57.43nF

** 实际焊接时，计算的理论参数无须严格遵守，轻微偏移并不会造成明显效率下降。

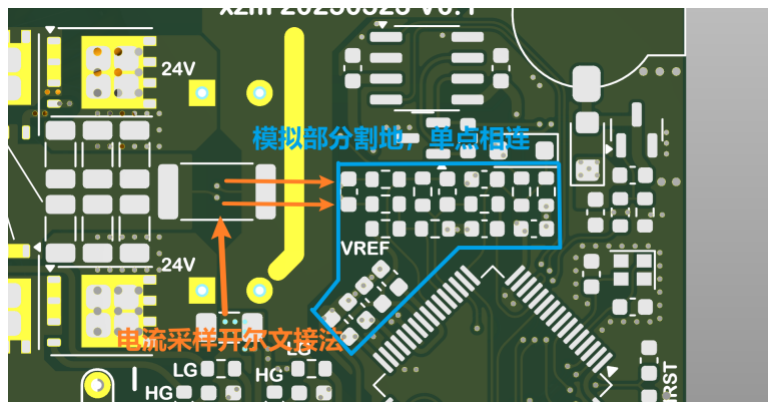
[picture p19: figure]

77 / 96

### 4.1.3 采样与反馈

采样与反馈部分需要采样全桥的电流和输入母线电压以计算发射端功率。与功率控制板相 似，无线充电发射端也充分利用了 STM32G4 的内置运放。

电压和电流采样

电压和电流采样都可以使用 MCU 内置运放实现，其中电压采样经过分压电阻和滤波电容后 进入运放跟随，随后进入 ADC 采样，而电流采样使用内部运放搭建差分放大器，参数如下：

- 放大倍数 25.5kΩ⁄1kΩ = 25.5V⁄V
- 偏置电压 2.9V⁄2 = 1.45V
- 理论量程绝对值 2.9V
2

÷ (2mΩ × 25.5V⁄V) = ±28.43A

- 理论分辨率 2.9V
4096

÷ (2mΩ × 25.5V⁄V) = 13.9mA

电压采样：

- 缩放倍率 (33kΩ + 2.2kΩ)⁄2.2kΩ = 16V/V
- 最大量程 2.9V × 16 = 46.4V
- | 一阶滤波截止频率： | 1
2π(33kΩ∥2.2kΩ)×3.3nF

≈ 23.38kHz

- ADC 理论分辨率：46.4V⁄4096 = 11.328mV

PCB 布局

78 / 96

### 4.1.4 辅助供电

辅助供电采用与功率控制板相同的配置，使用两个 RY8411 分别产生 10V 和 5V

为了进一步减小噪声，Buck 输入地与功率地相连，而数字地与功率地在 Buck 输出电容处 再相连。其它设计与功控板相似。
** 结合后续低位采样方案调试经验，模拟地与功率地在采样电阻处相连可以进一步减小共 模干扰对放大电路造成的影响。

79 / 96

### 4.1.5 ASK 解码电路

ASK 通讯通过将信息编码在线圈电压幅值上来进行反向通讯，解码电路共分为四个阶段。

峰值取样电路

考虑到线圈电压峰峰值最高可达 180V 左右，峰值取样电路使用两个 SS36 串联（与图中不 同，因为实测 1N4007 反向恢复过慢效果不佳），达到共 120V 的耐压。

通过分压电阻后向一个电容从进行充电，进行峰值取样，由于滤波截止频率较高，实际波形 在峰值附近有较大波动，此波动将在后级电路中滤波处理。

在运放输入端并联一个稳压二极管，防止电压过高损坏运放。

经过反复尝试，分压电阻选择 51kΩ和 4.7kΩ，电容选择 10nF

电压跟随器

对峰值取样电路的输出波形进行跟随，减小后级的输入阻抗，输出波形如下：

电压归中

滤除直流分量，并把信号的平均值限定在 1.45V 左右（参考电压一半）

高通滤波电阻取 240kΩ（等效 120kΩ），电容选择 10nF，截止频率在 100Hz 左右。

80 / 96

滤波放大电路

滤波放大电路的目标是滤除谐振频率的信号，只保留 8kHz 以下（ASK 通讯）的信号。使用

Multiple Feedback 架构的二阶有源滤波，使用 Analog Device 的 Analog Filter Wizard 进行 计算，设计结果如下：

滤波器参数如下：

运放的正输入端为输出的电压偏置，这里使用两个电阻对参考电压进行分压，输出偏置为 1.45V。输出结果如下图所示（此波形与 Qi 协议常规波形不同，下文会具体说明）：

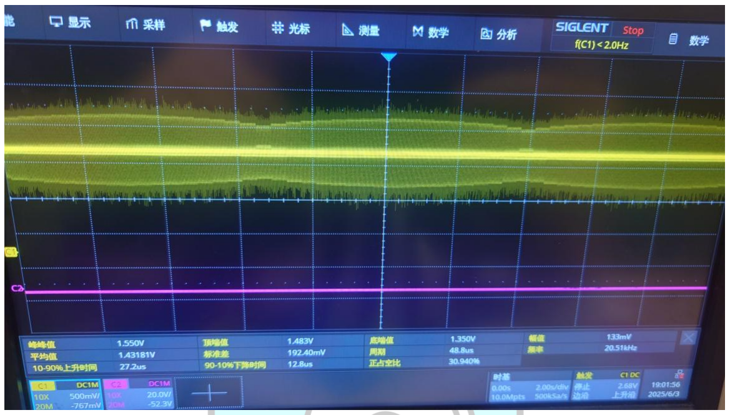
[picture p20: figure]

81 / 96

功率波动测试

为了测试通讯的稳定性，将发射功率在 10W-100W 间以 10W 步进反复切换，硬件解码电 路输出波形幅值波动较小，表现比较稳定：

### 4.1.6 功率级硬件配置

功率级通过移相全桥的方式实现输出功率的控制，通过 STM32474 的 HRTIM 进行控制。

HRTIM 配置与移相全桥实现

使用 TimerA 和 TimerB 分别控制两侧半桥的输出，固定占空比为 50%，通过 Master Timer 来动态控制两个子 Timer 的相位，实现中心对齐的移相全桥输出。

周期 148.5kHz，周期配置为 36633

使用 Master Timer 的 CMP1 和 CMP2 来触发两个子 Timer 的复位，例如当 CMP1 和 CMP3 都为 1/4 周期时，可实现相当于 0V 电压的输出

82 / 96

例如当 CMP1 和 CMP2 分别为 12.5%和 37.5%时，相当于激励电压为 24V*0.5=12V

例如当 CMP1 和 CMP2 分别为 0%和 50%时，相当于激励电压为 24V*1.0=24V

ADC 触发

为了最小化采样噪声，需要尽量避开开关时采样，所以目标为采集 1/2 处的量，使用 Master

Timer 的 CMP2 进行 ADC 采样的触发。

由于一阶滤波相位延迟 90°，在每周期的 3/4 处采样，对应 Counter 值为 27475，ADC 采

样时间为 12.5Cycle，为了最小化电流误差，应提前 6.25cycle 开始采样，ADC 频率为

170Mhz/4，6.25Cycle 对应 HRTIM 的 counter 偏移值为 800，故 CMP2 值为 27475-800。

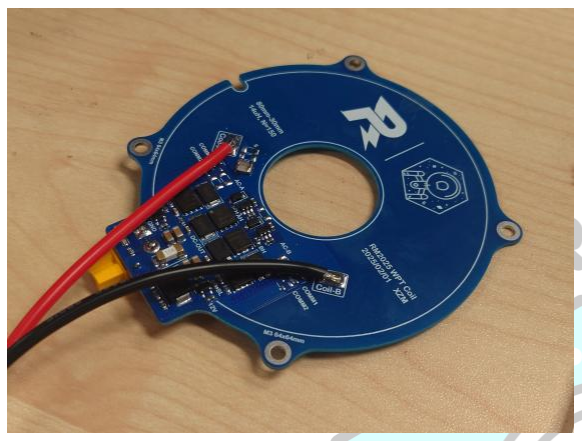
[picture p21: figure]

83 / 96

### 4.2 接收端

### 4.2.1 接收端线圈板

线圈板共进行两次迭代，第一版为主动全桥测试版（左图），由于测试发现主动全桥对效率 提升很小，所以在第二版删去了主动全桥电路（右图）。

主动全桥

主动全桥整流通过四个 UCC24612 同步整流控制器实现，如图所示为整流桥的一侧，参考 数据手册分别实现高位与低位的开关。但是后来测试后发现器对整体效率提升很小，且需要 提供 10V 供电（增大复杂度），整体收益较小，故在后续版本中移除。

** 由于隔磁片不能完全隔绝电磁感应，工作时线圈板铺铜部分温度可能较高（约 50-60°C）

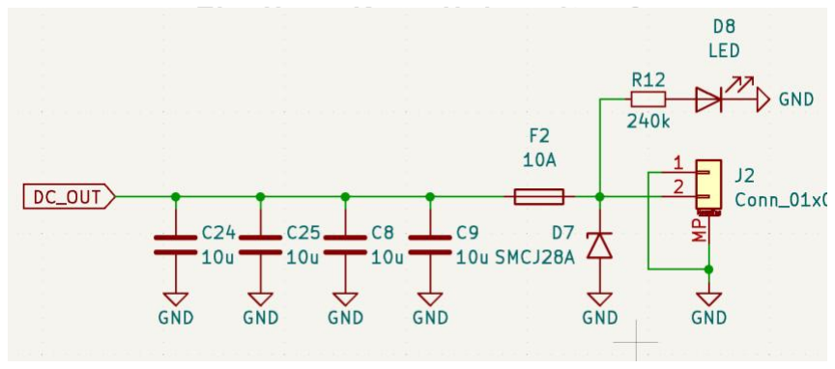
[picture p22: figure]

84 / 96

ASK 编码电路与谐振

串联谐振电容放置在线圈两端，这样设计是为了可以使用两个 50V 耐压谐振电容串联，等 效为一个容量减半的 100V 耐压电容以降低成本。

** 如电容耐压足够可以直接将另一组电容短接

ASK 编码电路通过放置两对不同大小的谐振电容，使得在功率较低时可以加大通讯信号的 幅值便于解码，但是实际测试中发现一对 6.8nF 电容已经可以实现稳定通讯。

开关 MOS 管使用 CJ2310，耐压 60V，最大电流 3A，防止击穿。

输出滤波

输出部分使用小电容+大电容的方式进行滤波和储能，并通过 TVS 和保险丝进行防护，当发 射端失控时，DC_OUT 电压升高，超过 TVS 击穿电压后会触发保险丝熔断保证输出安全：

** 输出需要容值较大的电容进行储能（如 220uF 固态电容），如已加入原理图中 1210 封 装的电容无需焊接，请避免焊接质量无法保证、参数明显不合理的电容

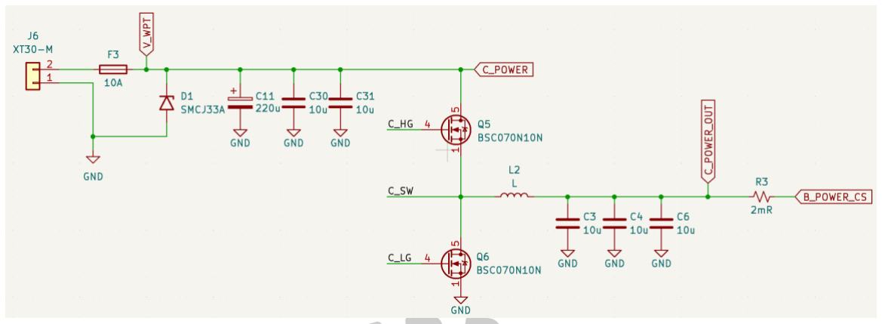
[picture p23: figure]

85 / 96

### 4.2.2 功率控制板无线充电部分

功率级

无线充电功率 Buck 电路使用 STM32G474 HRTIM 的 TimerE 进行控制。将无线充电全桥输 入降压给电容组充电。功率电路如图，其选型和控制等与功控板相似，不再详细说明。

当功率超过 145W 时，将触发功率过大的保护，具体方式为直接关断 ASK 的输出，从而使 发射端关断输出，具体通讯相关的内容将在后文具体说明。

86 / 96

## 4.3 控制与通讯算法

### 4.3.1 FSK 通讯

FSK 通讯通过发射端轻微改变谐振频率实现，接收端通过检测频率来解码信息。具体实现 上，接收端将接收线圈的一极经过电阻分压进入 STM32 内置的比较器比较，并通过比较器

输出触发一个 Timer 的 Capture Unit 进行采样，将当前的 Timer Counter 通过 DMA 传入一 个数组中。最后通过软件计算频率。

由于本设计的控制无需 FSK（即发射端到接收端的正向通讯），故仅对上述方法做了可行 性验证，并做了硬件预留。

### 4.3.2 ASK 通讯

ASK 通讯通过接收端开关通讯电容来影响发射线圈的幅值，并通过上文所示的 ASK 解码电 路解出通讯结果。

通讯格式

由于硬件原理限制，ASK 信道只能传输交流信号，本设计中直接使用 Qi 协议中的通讯格式：

如图，以 2kHz 的频率进行输出传输，每周期开始时进行一次电平翻转，如果 bit 为 1，在 周期一半时在进行一次翻转。

解码电路输出的解码方式

如上文中的波形图所示，本设计中的解码电路将信号的上升沿转化为上凸的波形，将下降沿 转换为下凹的波形，这与符合 Qi 协议的一般解码电路不同。

如图为 NXP 的 AN4701 中解码电路的输出，在开始处，由于隔直通交的截止频率过低等原 因，导致电压偏置回中值电压的速度过慢，此方法通过比较器可以直接获得源通讯波形相同 的波形，但是在调试过程中，发现此方式难以在功率变化时做到稳定解码；考虑到发射端

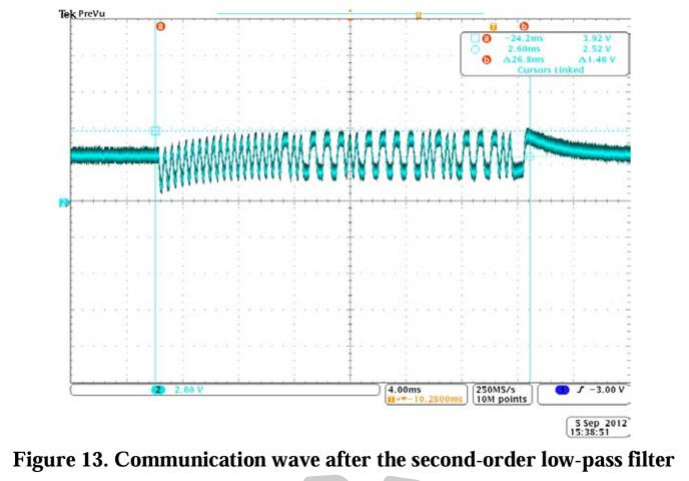
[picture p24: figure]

87 / 96

MCU 的负载较低，所以在本设计中直接通过快速的 ADC 采样来识别解码电路中的“上凸”

和“下凹”特性。

具体实现上，在高频环路中以开关频率的一半（主中断频率）采样解码电路的输出，当电压 大于或小于一定阈值时，对计数器进行累加，当计数器达到一个阈值，则认为电平翻转，最 终的解码效果非常稳定，波形如图（黄色波形为硬件解码电路输出，紫色波形为软件解码结

果输出）：

实习此效果的稳定阈值为：

uint16_t upperThreshold = 2310U; | // 上限阈值
uint16_t lowerThreshold = 1766U; | // 下限阈值
uint16_t cntThreshold = 6U; | // 连续采样次数阈值

88 / 96

数据包格式

为了保证整个无线充电系统的安全，接收端需要以尽可能快的频率进行功率反馈。本设计中 以 20bit 为周期（100Hz 频率），12bit 包长发送反馈数据。数据包格式如下：

其中橙色 12bit 代表数据包，蓝色代表有效数据，长度为 9bit。每个数据包中：

- 1bit 起始位（0）
- 9bit 数据位
- 1bit 校验位（如果 1 的个数为奇数则为 1）
- 1bit 停止位（0）

在解包时，通过识别固定不会变的波形（如图所示的紫色部分），特征为“8 个连续先高后 低的 1+一个双高的 0”即为起始位。

此格式最大化利用了包的长度，仅会出现一种情况导致误识别起始位（即上图中上面的数据 包），但此时解码得到的数据仍然可以保持结果相同。

有效数据内容

有效数据长度为 9bit，为了最大化功率反馈的精度以供发射端进行效率监测，将其中 8bit 用于传输功率信息。规定功率量程为 150W，将接收端读取到的 0-150W 数据映射到 0-255 的值上进行反馈。

剩余 1bit 用于接收端向发射端反馈开关需求，例如当电容组充满电时，此 bit 为 0，通知发 送端停止功率输出，仅输出最小功率维持通讯。

功率接收端/ASK 发射端编码

由于功率控制板中已有多个中断源，为了不引入额外的中断，将原有的 1kHz 低频中断改为 4kHz，1kHz 中断中的其他代码通过一个计数器分散到四次中断中运行。在 4kHz 的中断中， 每 40 次触发（100Hz）会触发一次打包。

打包时会首先将功率数据转化为 uint8，与开关 1bit 组合，并计算校验位

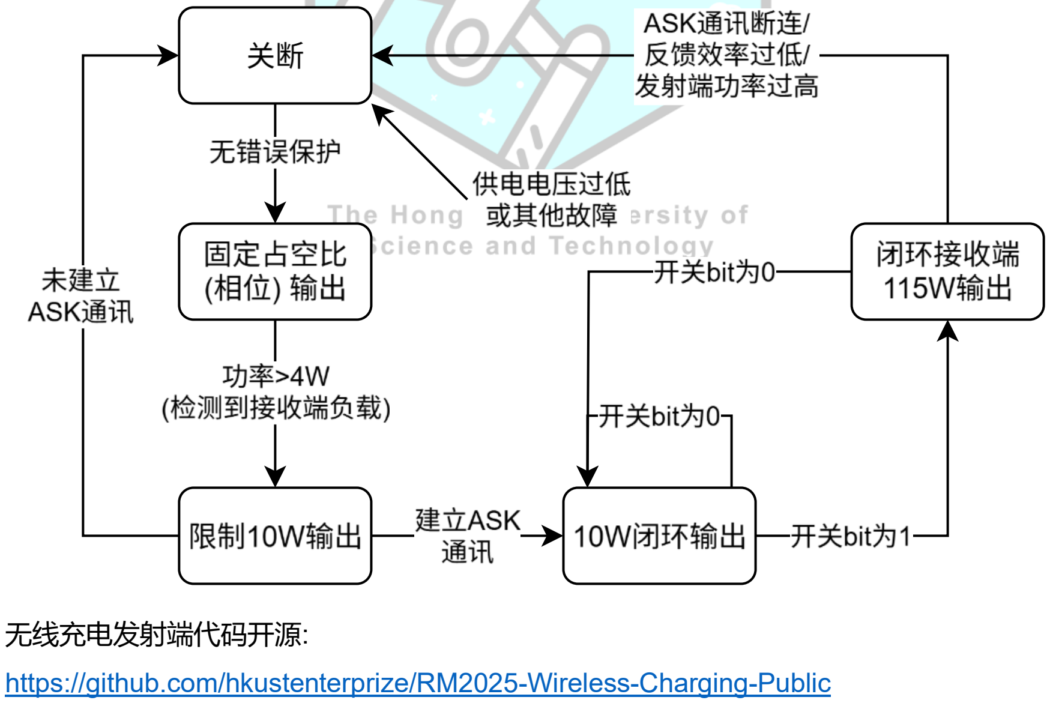
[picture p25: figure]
无线充电发射端代码开源:; https://github.com/hkustenterprize/RM2025-Wireless-Charging-Public

89 / 96

packedPower = (uint8_t)(wptPower * (255.0f/100.0f)); // 将功率转换为 0-255 范围
parity = (powerRequirement & 0b1) | (packedPower << 1);
parity ^= (parity >> 8);
parity ^= (parity >> 4);
parity ^= (parity >> 2);
parity ^= (parity >> 1);

askData.txMessage = 0x0
| (powerRequirement & 0b1) // 功率要求
| (packedPower << 1) | // uint8 格式的功率
| ((parity & 0b1) << 9); | // 奇偶校验
同时，通过写入 GPIO 的 BSRR 寄存器将输出拉高（开始时一定为高）

在之后每当 index 为偶数时进行一次 GPIO 翻转，当 index 为奇数时根据数据包内容判断是

否需要翻转。

功率发射端/ASK 接收端解码

接收端在通过 ADC 解码出信号的上升与下降沿后，通过 Timer 来获取脉冲长度，最终获得 1 或 0 的序列，寻找包头后即可解码出功率接收端的信息。

### 4.3.3 发射端状态机

## 5 迭代/测试记录

90 / 96

无线充电发射端 V1 功率传输测试，接收端功率 119.92W，效率 82.12%

功率控制板 V1（超级电容系统+无线充电接收端），与发射端 V1 共同测试功率传输

无线充电发射端 V1 与功率控制板 V1 的通讯测试

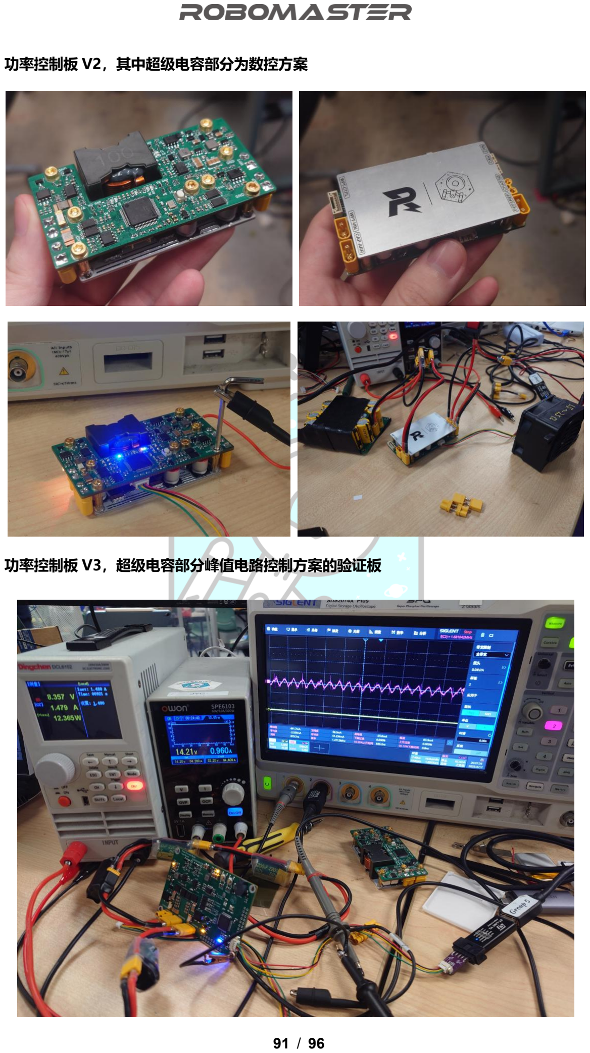
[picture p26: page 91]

91 / 96

功率控制板 V2，其中超级电容部分为数控方案

功率控制板 V3，超级电容部分峰值电路控制方案的验证板

92 / 96

无线充电发射端 V2 与线圈板 V2

功率控制板 V4

无线充电发射端 V2 与线圈板 V2、功率控制板 V4 进行通讯和功率测试

93 / 96

## 6 未来改进方向

由于本赛季研发压力较大，同时也需要负责工程机器人、英雄机器人相关 PCB 绘制与主控 板、哨兵交换机、新电池缓启动等项目的研发，整体研发时间较为紧张，所以尽管进行了多 次迭代，本方案仍有许多不足。

无线充电系统稳定性尚未得到充分验证

无线充电系统在一月末左右完成初代研发，但是因为综合考虑当时的规则，认为其收益很小 而放弃研发。在 5 月末青工会获知无线充电会加强后又重启研发，至六月初完成第二版的 全功能测试，在临近 UC 时才安装在机器人上进行测试。由于测试机会较少，所以其在机器 人上运行的稳定性目前还没有得到充分验证。

无线充电系统的相关理论计算不严谨

受限于本人的理论知识水平有限，且研发时间较短，对于无线充电，尤其是谐振计算部分， 本文和实际中的理论计算十分粗略，而对移相全桥相关的计算和发射端功率闭环也没有考虑 线性化等问题。在未来研发中将努力学习相关知识并学习工业中的成熟设计，将无线充电的 理论计算与实践过程更加严谨。

代码优化不足

由于在开始超级电容控制器和无线充电系统研发前为纯硬件，并没有大型嵌入式项目的开发 经验，C++代码相关知识也仅限于课本。这在很多时候导致写出的代码运行较为低效。未来 在逐步优化软件代码的同时，也会探索硬件提升运行速度的方式：例如本赛季曾经尝试过将

62.5kHz 环路的代码放入 STM32G474 的 CCMRAM 中运行；并且也有探索过使用 FMAC 进行电压环计算。在未来的开发过程中将会继续对它们的探索。

无线充电系统与超级电容系统融合有待改进

由于无线充电系统和超级电容系统同时随电容组进行充放电操作，其中的保护逻辑仍然有待 改进，例如当电容功率级关闭且无线充电发射端失控时（例如充电时被击杀导致底盘断电， 且发射端出现故障），会不可避免地造成保险丝熔断。

硬件方案并未进行深度优化

94 / 96

对于很多芯片的选型，例如 MOS 管、栅极驱动等，本赛季主要都沿用了上赛季电容控制器 的相似选型以求稳定，并节约开发时间。而对于一些参数的调整，例如功率 MOS 管的栅极 电阻大小、上升时间和死区等也未进行大量测试和精细调整。

无线充电接口短路风险

无线充电接口通过 Buck 电路向电容组接口输出。Buck 上管的提二极管会导致没有无线充 电的情况下电容组的电压灌入无线充电接口，当电容电压较快波动时（例如未连接电容组） 上电，体二极管会通过较大瞬时电流，多次后会损坏 MOS 管（表现为无法开启）。并且由 于无线充电接口需要延伸至线圈板，功率走线较长且比较靠外，增加了额外的短路风险，在 今后考虑通过加入背对背 MOS 等方式进行更充分的保护。

95 / 96

## 7 参考资料

[1] STM32 AN5306: Operational Amplifier (OPAMP) usage in STM32G4 Series
[2] STM32 RM0440: STM32G4 series advanced Arm®-based 32-bit MCUs
[3] STM32 AN5497: Introduction to the buck current mode with the

B-G474E-DPOW1 Discovery kit

[4] STM32 AN4539: HRTIM cookbook
[5] Qi Specification: Communications Physical Layer, Version 2.0 April 2023
[6] NXP AN4701: Demodulating Communication Signals of Qi-Compliant

Low-Power Wireless Charger Using MC56F8006 DSC

[7] 【RM2024 超级电容控制器硬件+软件完全开源】 (史上最详细的开源！)香港科技大

学 ENTERPRIZE 战队 https://bbs.robomaster.com/article/54127?source=4

[8] 【RM2023-数控超级电容方案开源】香港科技大学-ENTERPRIZE 战队

https://bbs.robomaster.com/article/9452?source=4

[9] STM32G474xB STM32G474xC STM32G474xE Datasheet

96 / 96

## 8 致谢

感谢 ENTERPRIZE 战队硬件组学长 JYC RY OFR 为硬件部门打下的坚实基础，并在本赛 季为超级电容与无线充电系统的设计调试中提供了巨大帮助

感谢 ENTERPRIZE 战队硬件组队员 ZZY 承担了大部分构建、调试发射端代码的工作

感谢吉林大学、中国石油大学（华东）、华南理工大学在交流中分享的宝贵经验

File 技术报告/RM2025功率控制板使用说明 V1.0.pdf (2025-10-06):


1 / 9

# 超级电容与无线充电系统使用说明

## RM2025 香港科技大学 ENTERPRIZE 战队

2025/10/06 V1.0

2 / 9

目录

版本记录

V1.0 | 第一版使用手册 | 2025/10/07


3 / 9

# 1. 硬件焊接

## 1.1 下板焊接注意事项

推荐焊接顺序为：

- 焊接贴片元件
- 焊接排针，注意要尽可能准地对齐，且尽可能垂直朝上
- 电容、2923 电感最后焊接
- 在无线充电 Buck 的上管并联焊接一个肖特基二极管，这一步是为了防止在电容端悬空、 电压快速上升时，电容端通过 Buck 上管的体二极管给无线充电端电容充电，瞬时电流 过大导致上管损坏，表现为无法达成较高占空比或无法打开。如图：

## 1.2 上板焊接注意事项

焊接上板推荐顺序为：

- 焊接贴片元件
- 验证 MCU 功能
- 将排母插至下板，叠加上板，以便对齐焊接

上板可以使用 SMT 来减小工作量，只贴片电阻电容成本较低且可以显著提高稳定性


4 / 9

# 2. 开发环境

开发环境沿用了 RM2024 开源中使用的工具链，也是在 ENTERPRIZE 队里通用的开发工

具链：

- 工具链与 IDE 使用了 STM32CubeMX + GCC + VSCode.
- STM32CubeMX 能够帮助生成 Makefile 文件、LinkerScript 文件

工程中 SuperCap.mk 使得代码可以使用 C++编写，同样也是沿用了队里的配置方法。

# 3. 基本硬件连接

功率控制板的基本连接方式如图：

5 / 9

- 烧录接口：与大疆 C 板相同，为不带锁的 4Pin 接口
- 无线充电信号接口：带锁的 GH1.25 接口，与无线充电线圈板连接
- 底盘输出：XT30 母头，连接底盘电机
- 电管输入：XT30 公头，连接电源管理模块的 Chassis 接口
- 无线充电：XT30 公头，连接无线充电线圈板的 XT30 输出接口
- 电容组：XT30 公头，连接电容组（电容管理模块 CM01 的输入接口）

除了无线充接口外，其他 XT30 接口内部都接有 SMCJ28A TVS，击穿电压为 34V 左右。

实际调试中，当接有感性负载（如 M3508 电机），输入接口一定要使用电池供电，如果使 用可调电源供电，电流无法倒灌，会有烧毁 TVS 的风险，现象为输入短路。

无线充电接口接有 SMCJ33A，击穿电压相对较高，实际使用中该接口设计在 30V 一下运行。

# 4. 硬件调试流程

## 4.1 首次上电

首次上电前，需要通过万用表通断当测量各电源网络短路情况：

- 各 XT30 接口，10V、5V、3.3V、3.3VA 电源

接入可调电源（任意 XT30 接口），将限流调整为 0.1A，电源从 4.0V 左右逐渐上升，此时

观察 3.3V 网络和 3.3VA 网络的电源是否正常

将电压从 5.0V 左右缓慢上调，观察 5V 网络的电压是否正常

将电压从 10V 左右缓慢上调，观察 10V 网络的电压是否正常

测试电源过程中，如果一切正常，可调电源应该不会出现限流的情况。

如果有条件，二元使用示波器观察 5V 和 10V 的输出纹波（一般不需要）。


6 / 9

## 4.2 首次烧录代码

断开所有 XT30 供电，插入调试器，使用 VSCode 打开工程，在终端中输入 make -j，编译

成功后应有绿色的 Build success 提示

打开 ozone，创建工程

文件选择 /build 文件夹中的 .elf 文件

点击左上角的绿色按钮，弹出窗口点击 accept

代码运行后，在 Watched Data 窗口添加 sysData，右键 Refresh Rate 选择 5Hz，如果代 码正常运行可以观察到 vTick 变量增加（单位 ms）


## 4.3 首次上电

首先保证关键硬件选型与开源一致（例如采样电阻、放大器倍数、晶振频率等）

在 Core/Inc/Calibration.hpp 中将 CALIBRATION_MODE 解除，再次编译烧录

在 Watched Data 窗口添加 adcData，将裁判系统 XT30 接口供电 24V，限流 0.1A，电容组 XT30 接口接入电子负载，尝试通电，如果输出电源为 28.8V 左右即可

观察 adcData 中的 vA、vB、vWPT 应该都有度数

将限流调大，尝试开启负载（0.5A 左右），观察功率损耗不会过大，功控板没有明显发热


7 / 9

再次将限流调大至 3A 左右，负载恒流模式逐渐加大，可观察到可调电源功率不会超过 37W， 此时 iA、iB 应该都有合理读数

## 4.4 校准电压

在 CALIBRATION_MODE 定义时，adcData 中会有 tempData 变量，分别为 iA、iR、vA、

iB、vB、iWPT、vWPT 的 ADC 原采样值的四倍（四次采样累加）

将裁判系统接口、电容组接口、无线充电接口分别接入可调电源，调整可调电源的电压，将 对应原始数据记录在 Excel 中：

记录数据后，下边的图表应该近似为一条直线，R^2 应该为 1 或 0.99 左右，说明校准值较 为合理

在 Core/Inc/Calibration.hpp 中仿照示例复制一份新的校准参数，将 Excel 表格中拟合出的 斜率和截距复制进去（注意需要复制完整的数值，包括很多位小数点），注意：

- 粘贴进去的值应与原来的示例值相近，符号一致
- 小数后面需要加入 f


8 / 9

## 4.5 校准电流

在 Ozone Watched Data 窗口中添加 psData

调整恒流负载值，使输出电压约为输入电压的 0.8 倍，将 psData.dcdcMode 改为 5 (CALIBRATION_B)，断开负载，此时输出电压应该稳定在输入电压的 0.8 倍左右

调整负载电流，记录 iB 的 ADC 原始数据和实际数据（如有外置较为精准的电流表更好，使 用可调电源和可调负载的读数也可以）

重跑代码，调整恒流负载值，使输出电压约为输入电压的 1.25 倍，将 psData.dcdcMode 改为 4 (CALIBRATION_A)，断开负载，此时输出电压应该稳定在输入电压的 1.25 倍左右

调整负载电流，记录 iA 和 iR 的 ADC 原始数据和实际数据（如有外置较为精准的电流表更 好，使用可调电源和可调负载的读数也可以）

在 Core/Inc/Calibration.hpp 中仿照示例复制一份新的校准参数，将 Excel 表格中拟合出的 斜率和截距复制进去（注意需要复制完整的数值，包括很多位小数点），注意：

- 粘贴进去的值应与原来的示例值相近，符号一致
- 小数后面需要加入 f
- 电流的误差可能较大（R^2 值可能在 0.98-1），精度低于电压采样，这是正常现象

## 4.5 应用校准参数

记录 Ozone Watched Data 窗 口 中 sysData.hardwareUID 的 值， 将其 复制到

Core/Inc/Calibration.hpp 中的 HARDWARE_UID_W0-W2

再次检查校准值与示例校准值相近且正负号一致，重新编译代码，烧录

此时从 adcData 中观察到的读数应该较比之前较为准确。


9 / 9

# 5. 无线充电发射端线圈绕制

1. 采用 T141-2 羰基铁粉芯磁芯（外径 36*内径 11 厚度 11mm），0.1*200 股利兹线，以 目标绕制 6.8uH 左右的谐振电感为例，需要准备 1 米左右的利兹线
2. 将利兹线绕制 20 圈左右，绕制时需要保证线较紧，分布均衡，两面留出较长余量
3. 给利兹线末端上锡：将利兹线使用金属台钳夹住（保证散热快，防止将过长的绝缘层烧 毁），露出 1cm 左右，建议使用较大的刀头烙铁调至 400°C 进行上锡
4. 使用 LCR 电桥测量感值并调整绕制圈数，当调整至目标感值附近时将利兹线和磁芯打 胶固定（例如使用 UV 胶），将两端线头剪短，重复上锡步骤
5. 最后将整体线圈焊接在 PCB 板上，将线圈主体与 PCB 板打胶固定，在调试好功能后 （比较确定之后不再需要修改）建议对焊点即焊点延伸出的线也进行打胶固定。

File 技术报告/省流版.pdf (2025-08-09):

# 超级电容与无线充电系统


RM2025 香港科技大学 ENTERPRIZE战队 2025/08/05

# 主要分享内容

超级电容系统
1. 发展方向展望
2. 系统总览
3. 峰值电流控制模式
4. 上管常开实现思路分享
5. 保护
6. 电容组

无线充电系统
1. 系统总览
2. 功率传输
3. 反向通讯

# 超级电容：发展方向展望

经过多年的发展，在各参赛队的努
力与分享中，超级电容系统已经发
展得较为成熟。
本赛季新引入的总能量限制，对超
级电容系统提出了一些新的要求
（例如：更高的效率），但对系统
本身没有很大影响。
同时，超级电容作为UC赛场上的
“标配”，对稳定性有着极高的要

求，优先级高于对性能的极致追求。

# 超级电容：发展方向展望


本赛季的核心目标：保下限，提上限


保下限：硬件到代码的全方位保护、追求极致的稳定性
提上限：更快的响应速度、更高的效率、更小的体积…

例如我队23-24年开源的超级电容系统有着绝对的稳定性：

# 超级电容：系统总览


4*XT30：裁判系统输入、底盘输出、电容组、无线充电输入 CAN接口、烧录接口、无线充电通讯接口

体积 60x44x30mm
集成无线充接收端降压
峰值电流控制模式
四管双向 Buck-Boost
250k开关 62.5k外环

# 超级电容：控制需求

超级电容系统需要控制什么？

电容组; 裁判系统

通过动态调整电容组的输入/输出功率来
保证裁判系统端不超过功率上限

即需要通过控制超级电容系统支路的电流
（可以是DCDC输入/输出或电感电流）

# 超级电容：控制方式

数控方式：

采样实际电流电压 > 环路计算 > 占空比 > 作用于电容电流

优点：稳定可靠，硬件和软件实现都比较简单

缺点：比较依赖计算资源，提升响应一般需要提升运算频率

峰值电流：通过模拟环路直接控制电感峰值电流，随后作用于电容电流

# 超级电容：峰值电流控制

以Buck转换器（CCM）为例，运行方式如下：


# 超级电容：峰值电流控制


Buck-Boost实现：在电容后进行高位采样，上管打开时采样电流即为电感电 流，选取一侧的电流波形对对侧进行峰值电流控制，本侧保持固定占空比。

# 超级电容：峰值电流控制


Buck-Boost实现：

为了实现升降压，需要切换两侧半桥
的开关行为

为了尽量避免共模变化的影响，需要
切换峰值电流控制源

共有四种模式，通过检测到的占空比
进行切换

# 超级电容：峰值电流控制

占空比检测通过采样两端电压实现，考
虑到其有误差并且为了保持一定冗余，
运行中每个模式实际允许的占空比更大
工作模式 | A侧半桥 (底盘 /裁判系统) | B侧半桥 (电容 组)
Buck | 受B侧峰值电流 控制 | 常开


BuckBoost (Vin>Vout) | 受B侧峰值电流 控制 | 固定84%占空 比
BuckBoost (Vin<Vout) | 固定84%占空 比 | 受A侧峰值电 流控制
Boost | 常开 | 受A侧峰值电 流控制

Buck模式（iB谷值电流）; Buck-Boost (Vin > Vout) 模式（iB谷值电流）

到此为止，我们已经获得了一个响应极快且无需计算资源的峰值电流内环， 数字外环仅需给出电感峰值电流的目标值即可控制整个系统。

# 超级电容：电流环响应速度

在PID参数留有一定余量的情况下，输出电流的响应（经过500uF左右的滤波 电容）可达20μs级别。测试中使用电流探头测量输出，每50ms改变一次目标 值，阶跃1.5A左右：


上曲线为裁判系统功率，下曲线为 | 功率（方便观察在绘图时加了-120W的
偏置）。测试使用四个3508电机的 | ，加速并突然急停，如图可见裁判系统
端功率很好地完成了闭环，并几乎将全部的刹车的反冲能量导入了电容中


# 超级电容：上管常开


由于MOS的GS间会漏电，所以要实现上管常开需要加入特殊的电路，我们 过去使用了隔离电源，本赛季使用了撰写23年开源的学长提出的类似电荷泵 的结构，仅需加入右图中的电路即可实现。这种方式较比隔离电源减小了静 态功耗（工作时整个控制器仅1W左右）。

# 超级电容：保护

由于电容组中存有2000J能量，超级电容系统故障很可能导致比较严重的后 果，所以本赛季超级电容也设计了全面且严格的保护措施。

过流/过压保护：ADC采样 > AWDG硬件触发关断

短路保护：电流大于一定值且电压小于一定值，触发关断

电容组漏电/断连保护：电压或电荷量达到一定阈值计算等效容量

CAN断连保护、电池低电量报警、效率检测、电容电流限制、错误处理与自 恢复……

# 超级电容：电容组


特点就是很小，可以完全塞到装甲板后面，
能省很多空间，别的没啥特殊的

# 无线充电：系统概览

为了简化硬件设计和接线难度，将无线充电 接收端的相关电路与超级电容系统融合，在 同一块MCU上实现。; 功率传输部分使用LCC-S拓扑，激励源选择 全桥逆变，接收端的功率变换器选择Buck架 构，将整流桥输出降压输入到超级电容中。; 无线充电握手部分，选择通过模仿较为成熟 的Qi协议的方法，通过FSK和ASK实现。

# 无线充电：发射端

主要电路：
-功率级（全桥逆变）
-谐振电路
-采样与反馈电路
-辅助供电

-ASK解码
MCU选用与功率控制板上相同的
STM32G474RBT3，输入为24V，并预留有24V输 出接口与CAN通讯电路（如果对位机构需要电机）

# 无线充电：功率级


发射端：全桥逆变+LCC谐振 | 接收端：S谐振+全桥整流

# 无线充电：接收端（功控板部分）

在全桥整流输出后，通过数控Buck电路将其降压至电容组电压（最大28.8V）。

由于有供电电压30V的限制，需要通过一些特殊方式实现接近100%的占空比


# 无线充电：反向通讯

功率接收端：两对通讯电容 | 接收端需要以尽可能快的频率进行功率反馈。以20bit 为周期（100Hz频率），12bit包长发送反馈数据。


8bit 功率反馈

1bit 功率需求(是否满电)

（应对不同功率下的幅值变化）


# 无线充电：反向通讯

功率发射端解码电路：
峰值检测 > 电压跟随 > 高通滤波 >

二阶低通滤波 > ADC解码波形 >
解码数据包

# 无线充电：状态机

功率发射端状态机; 功率接收端状态机

# 无线充电效果展示


【复活赛寄了，可以发了 (https://www.bilibili.com/video/BV1kU8GzAEFH/) 之无线充电】 (https://www.bilibili.com/video/BV1kU8GzAEFH/)

# 无线充电安装


致谢

感谢 ENTERPRIZE 战队硬件组学长 JYC RY OFR 为硬件部门打下的坚实基础， 并在本赛季为超级电容与无线充电系统的设计调试中提供了巨大帮助

感谢 ENTERPRIZE 战队硬件组队员 ZZY 承担了大部分构建、调试发射端代 码的工作

感谢吉林大学、中国石油大学（华东）、华南理工大学在交流中分享的宝贵 经验

感谢 RoboMaster 为青年工程师提供的平台

## ENTERPRIZE战队 25赛季开源预告

硬件：
- 超级电容与无线充电系统
- G4主控板V2、工程主控板
- 无线烧录器
算法：
- 局均1600s最高1900s 单目视觉雷达站算法 机械：
- 5.8秒4级矿 舵轮机械臂工程机器人
- 自制3508气泵+吸矿状态检测滤波算法
- 中供弹过洞舵轮英雄+42mm中心供弹
- 串联腿步兵开源
- CNC舵轮方案、低成本3508减速箱
- 全直驱过洞麦轮步兵机器人


非常感谢各位对香港科技大学 ENTERPRIZE 战队开源项目的关注与支持。若您在机器人设计过 程中受益于我们的开源，恳请在开源引用中注明我们的项目来源。大家的支持是我们不断前行的 动力。让我们携手共建一个鼓励创新、协作与超越的 RM 开源生态。

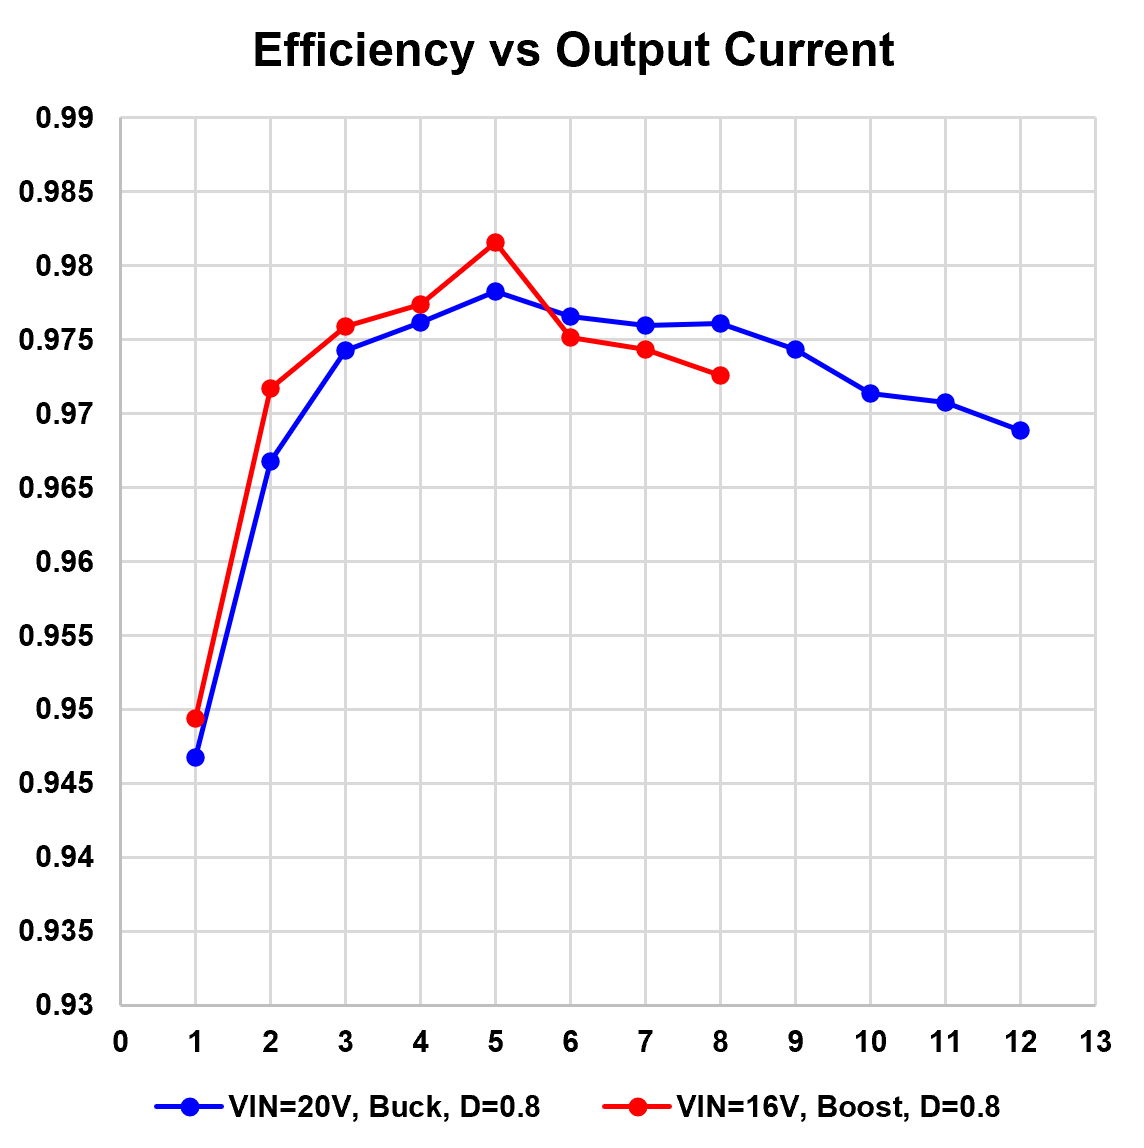
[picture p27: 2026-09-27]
efficiency.png

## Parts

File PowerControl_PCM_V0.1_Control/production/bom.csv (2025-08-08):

Designator | Footprint | Quantity | Value | LCSC Part #
BZ2 | Buzzer_5020 | 1 | Buzzer_5020
C1, C2, C32, C33, C43, C44, C45, C47, C9 | 0603 | 9 | 3n3
C10, C29, C34, C35, C39, C40, C41, C62, C63, C64, C65, C66, C72, C73, C87, C88, C96 | 0603 | 17 | 100n
C36, C37, C38, C42, C46, C79 | 0805 | 6 | 22u
C48, C49, C50, C74, C85, C86, C90, C94, C95 | 0603 | 9 | 4u7
C67, C68, C69, C70 | 1206 | 4 | 10u
C75, C77, C78, C89, C91 | 0603 | 5 | 20p
C92, C93 | 0603 | 2 | 10n
D12 | SOT-23 | 1 | ESD1CAN
D13, D14, D27 | WS2812B-2020 | 3 | WS2812B-2020
D15 | 0603 | 1 | 3V3
D18, D21, D7, D8 | D_SMF | 4 | K34
D19 | 0603 | 1 | EH
D20 | D_SMF | 1 | SMF3V3A
D22 | 0603 | 1 | AH
D23 | 0603 | 1 | AL
D24 | 0603 | 1 | BH
D25 | 0603 | 1 | BL
D26 | 0603 | 1 | EL
F4, F5, F6 | 1206 | 3 | 1A 1206
J1 | Molex_PicoBlade_53261-0471_1x04-1MP_P1.25mm_Horizontal | 1 | SWD
J10, J11, J17, J18, J19, J8, J9 | PinSocket_2x02_P2.00mm | 7 | Conn_F
J20, J21 | JST_GH_BM02B-GHS-TBT_1x02-1MP_P1.25mm_Vertical | 2 | CAN3
J22 | JST_GH_BM04B-GHS-TBT_1x04-1MP_P1.25mm_Vertical | 1 | Conn_01x04_MountingPin
L1, L4 | L_Sunlord_SWPA3015S | 2 | 4u7
Q11 | SOT-23 | 1 | SI2300
R1, R40, R43, R45, R47, R48, R49, R50, R51 | 0603 | 9 | 10k
R15, R16, R17, R18, R19, R20, R25, R26, R27, R32, R33, R58, R59, R60, R61, R64 | 0603 | 16 | 2k2
R21, R28, R29, R30, R31, R39, R41, R46, R52, R53, R54, R55, R57, R62 | 0603 | 14 | 120R
R22, R23, R24, R63 | 0603 | 4 | 33k
R36, R56 | 0603 | 2 | 1k
R42 | 0603 | 1 | 118k
R44 | 0603 | 1 | 53k6
SW3 | Button_PTS810 | 1 | BTN
TH1 | 0603 | 1 | Thermistor_NTC
TP1, TP2, TP3, TP4, TP5, TP6, TP7, TP8, TP9 | TestPoint_Pad_D1.0mm | 9 | TestPoint
U12 | LQFP-64_10x10mm_P0.5mm | 1 | STM32G474RBTx
U13, U14 | SOT-23-6 | 2 | RY8411
U16, U17 | SOT-23-5 | 2 | RS3236
U4, U6, U7, U8 | TSSOP-8_4.4x3mm_P0.65mm | 4 | INA240A1PW
U5 | SOIC-8_3.9x4.9mm_P1.27mm | 1 | TJA1042T-3
Y1 | Crystal_SMD_2016 | 1 | 25Mhz_2016

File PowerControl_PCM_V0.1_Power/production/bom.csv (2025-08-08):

Designator | Footprint | Quantity | Value | LCSC Part #
C1, C2 | 0603 | 2 | 1n
C11, C13, C14, C23, C24 | C_D8.0mm_P3.50mm | 5 | 220u
C12, C25, C27, C28, C5 | 0603 | 5 | 4u7
C15, C16, C17, C18, C19, C20, C21, C22, C3, C30, C31, C4, C6 | 1206 | 13 | 10u
C26, C7, C8 | 0603 | 3 | 100n
D1 | D_SMC | 1 | SMCJ33A
D10, D2 | D_SOD-323_HandSoldering | 2 | BZT52C11S
D11, D9 | SOT-23 | 2 | BAV99
D5, D6 | D_SMC | 2 | SMCJ28A
F1, F2 | Fuse_Littelfuse-NANO2-451_453 | 2 | 30A
F3 | Fuse_Littelfuse-NANO2-451_453 | 1 | 5A
J12, J13, J14, J15, J16, J3, J7 | PinHeader_2x02_P2.00mm_Vertical_SMD | 7 | Conn_M
J2 | AMASS_XT30U-F_1x02_P5.0mm_Vertical | 1 | XT30-F
J4, J5, J6 | AMASS_XT30U-M_1x02_P5.0mm_Vertical | 3 | XT30-M
L2 | L_Wuerth_HCI-1040 | 1 | L
L5 | L_VER2923 | 1 | 10uH
Q1, Q2, Q3, Q4, Q5, Q6 | TDSON-8-1 | 6 | BSC070N10N
R1, R2, R4, R5, R6, R7 | 0603 | 6 | R_Gate
R10, R3, R8, R9 | 2512 | 4 | 2mR
R11, R12, R13, R14 | 0603 | 4 | 4k7
U1 | SOIC-8_3.9x4.9mm_P1.27mm | 1 | UCC27201A
U2, U3 | SOIC-8_3.9x4.9mm_P1.27mm | 2 | UCC27211

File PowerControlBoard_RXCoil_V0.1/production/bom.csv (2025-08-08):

Designator | Footprint | Quantity | Value | LCSC Part #
C1, C16, C17, C18, C19, C2, C3, C4 | 1206 | 8 | C_s
C10, C11 | 1206 | 2 | C_comm2
C12, C13, C14, C15 | 0603 | 4 | 330p
C20, C21, C22, C23 | 1210 | 4 | C
C24, C25, C8, C9 | 1206 | 4 | 10u
C5, C6 | 1206 | 2 | C_comm1
C7 | 1206 | 1 | C_det
D1, D10, D2, D3, D4, D5, D6, D9 | D_PowerDI-5_3D | 8 | SB2060L
D7 | D_SMC | 1 | SMCJ28A
D8 | 0603 | 1 | LED
F2 | Fuseholder_Littelfuse_Nano2_157x | 1 | 10A
J1 | JST_GH_SM04B-GHS-TB_1x04-1MP_P1.25mm_Horizontal | 1 | WPT
J2 | AMASS_XT30PW-F_Horizontal | 1 | Conn_01x02_MountingPin
Q1, Q2, Q7, Q8 | SOT-23 | 4 | CJ2310
R1, R2, R3, R4 | 0603 | 4 | 100R
R10, R9 | 0603 | 2 | 33R
R11 | 0603 | 1 | 100k
R12 | 0603 | 1 | 240k
R5 | 0603 | 1 | 10k

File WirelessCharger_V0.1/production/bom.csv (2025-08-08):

Designator | Footprint | Quantity | Value | LCSC Part #
BZ1 | MLT-9032 | 1 | Buzzer
C1, C2, C43, C51, C52, C59, C60, C67, C71, C77, C78 | 0603 | 11 | 4u7
C10, C34, C35, C5, C6, C62, C63, C7, C8, C9 | 1206 | 10 | 10u
C11, C12, C13, C14, C21, C26, C81, C82, C83, C84 | C_Rect_L11.0mm_W5.1mm_P10.00mm_MKT | 10 | ?
C15, C56, C57, C58 | 0603 | 4 | 10n
C16, C17, C74 | 0603 | 3 | NC
C18 | 0603 | 1 | 13n
C19 | 0603 | 1 | 80p
C20 | 0603 | 1 | 3n3
C22, C23, C45 | 0603 | 3 | 20p
C24 | 0603 | 1 | 10u
C25, C27, C28, C29, C31, C33, C49, C50, C53, C55, C64, C65, C68, C75, C76 | 0603 | 15 | 100n
C3, C4 | 0603 | 2 | Cbst
C30, C38 | CP_Radial_D8.0mm_P3.50mm | 2 | 220u
C32, C39, C40, C41, C42, C44, C46, C47, C48, C54, C61, C66 | 1206 | 12 | ?
C36, C37, C69, C70, C72, C73 | 0805 | 6 | 10u
D1, D4 | D_SOD-123F | 2 | BZT52C3V3S
D17, D5 | D_SMF | 2 | K34
D18 | 0603 | 1 | 3V3
D19 | 0603 | 1 | 5V
D2, D3 | D_SMF | 2 | 1N4007
D20 | 0603 | 1 | 12V
D22 | 0603 | 1 | CHA1
D24 | 0603 | 1 | CHB1
D6 | SOT-23 | 1 | ESD1CAN
D7, D8 | WS2812B-2020 | 2 | WS2812B-2020
D9 | D_SMC | 1 | SMCJ28A
F1 | Fuse_Littelfuse-NANO2-451_453 | 1 | Fuse
F2, F3 | 1206 | 2 | 1A 1206
H10, H6, H7, H9 | MountingHole_3.2mm_M3_DIN965_Pad | 4 | GND
H13 | TestPoint_Plated_Hole_D2.0mm | 1 | Coil_N
H8 | TestPoint_Plated_Hole_D2.0mm | 1 | Coil_P
J1 | AMASS_XT30U-F_Vertical | 1 | Coil
J2 | AMASS_XT30U-M_Vertical | 1 | Conn_01x02
J3 | JST_PH_B2B-PH-SM4-TB_1x02-1MP_P2.00mm_Vertical | 1 | 10V
J5 | AMASS_XT30U-F_Vertical | 1 | Conn_01x02
J6 | Molex_PicoBlade_53261-0471_1x04-1MP_P1.25mm_Horizontal | 1 | SWD
J7, J8 | JST_GH_BM02B-GHS-TBT_1x02-1MP_P1.25mm_Vertical | 2 | CAN3
J9 | JST_PH_B2B-PH-SM4-TB_1x02-1MP_P2.00mm_Vertical | 1 | WLED
L1 | L_90125_3P | 1 | Lp
L4, L5 | L_Sunlord_SWPA3015S | 2 | 4u7
Q1, Q3, Q5, Q6 | TDSON-8-1 | 4 | BSC070N10NS3G
Q2, Q4, Q7 | SOT-23 | 3 | AO3400A
R1, R2, R4, R5 | 0603 | 4 | RGate
R10, R6, R7 | 0603 | 3 | 51k
R11 | 0603 | 1 | 25k5
R12, R13, R19 | 0603 | 3 | 100k
R14 | 0603 | 1 | 10nF
R15, R16, R20, R21, R3 | 0603 | 5 | 4k7
R17, R22, R23, R24, R27, R31, R42, R43, R46, R47, R48, R51, R52, R53 | 0603 | 14 | 120R
R18 | 1206 | 1 | R
R25, R28, R29, R38, R40, R44, R45, R49 | 0603 | 8 | 10k
R26, R30, R34, R55 | 0603 | 4 | 2k2
R32, R8, R9 | 0603 | 3 | 1k
R35 | 2512 | 1 | 2mR
R37 | 0603 | 1 | 118k
R39 | 0603 | 1 | 53k6
R41, R50 | 0603 | 2 | 0R
R54 | 0603 | 1 | 33k
SW1, SW3 | Button_PTS810 | 2 | BTN
SW2 | Button_PTS810 | 1 | NRST
TP1, TP2 | TestPoint_Pad_D1.5mm | 2 | TestPoint
U1, U2 | SOIC-8_3.9x4.9mm_P1.27mm | 2 | UCC27211DRM
U10, U11 | SOT-23-5 | 2 | RS3236
U12, U13 | SOT-23-6 | 2 | RY8411
U3 | SOIC-8_3.9x4.9mm_P1.27mm | 1 | TJA1042T-3
U5 | SOIC-8_3.9x4.9mm_P1.27mm | 1 | GS8552-SR
U9 | LQFP-64_10x10mm_P0.5mm | 1 | STM32G474RBTx
Y1 | Crystal_SMD_2016 | 1 | 25Mhz_3225

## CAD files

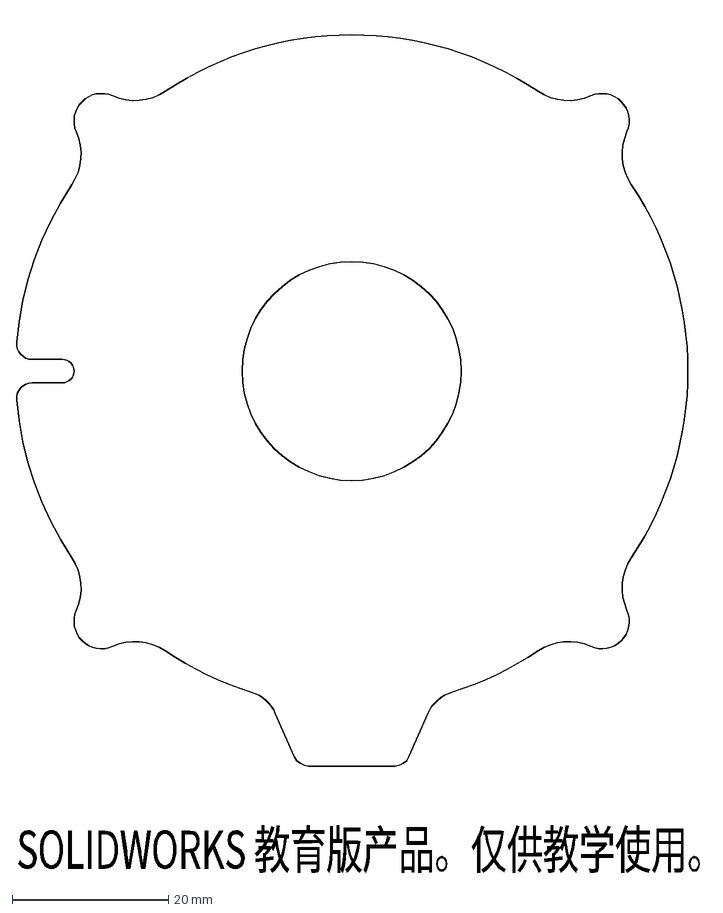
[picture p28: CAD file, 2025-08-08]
PowerControlBoard_RXCoil_V0.1/CoilBoard.DXF
SOLIDWORKS 教育版产品。仅供教学使用。

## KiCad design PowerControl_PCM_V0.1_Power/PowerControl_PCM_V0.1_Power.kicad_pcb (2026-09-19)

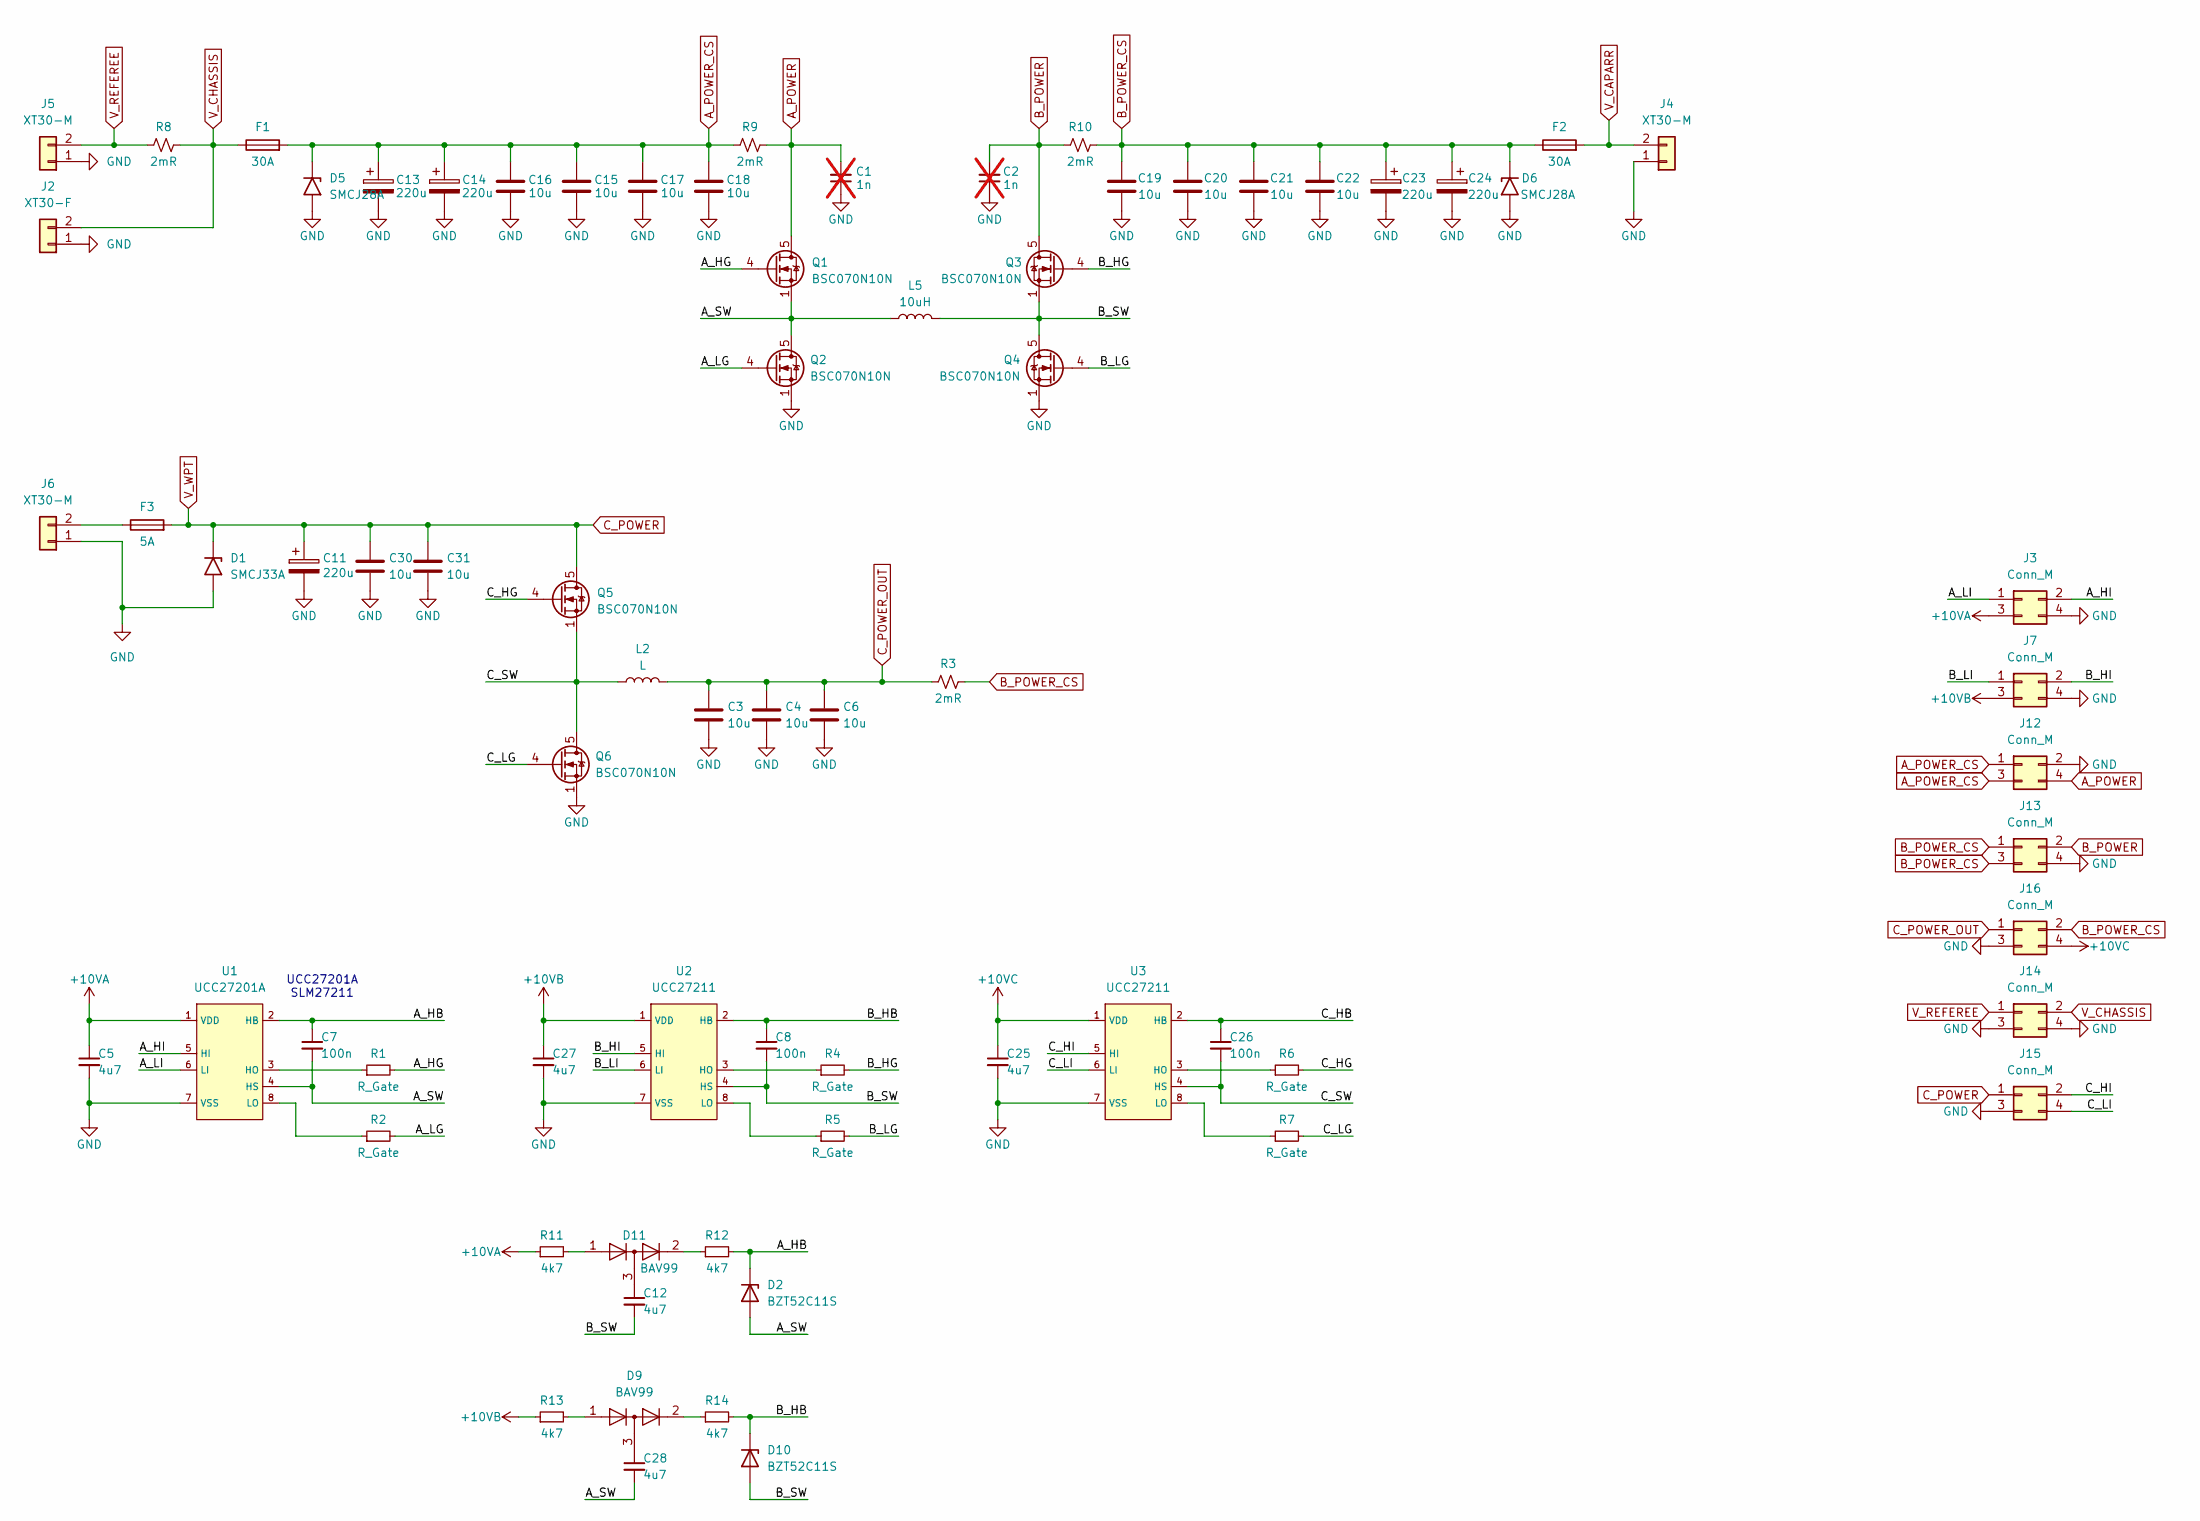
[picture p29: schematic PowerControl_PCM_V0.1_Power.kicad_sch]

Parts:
C1, C2: 1n; C_0603_1608Metric; not fitted
C3, C4, C6, C15, C16, C17, C18, C19, C20, C21, C22, C30, C31: 10u; C_1206_3216Metric
C5, C12, C25, C27, C28: 4u7; C_0603_1608Metric
C7, C8, C26: 100n; C_0603_1608Metric
C11, C13, C14, C23, C24: 220u; C_D8.0mm_P3.50mm
D1: SMCJ33A; D_SMC
D2, D10: BZT52C11S; D_SOD-323_HandSoldering
D5, D6: SMCJ28A; D_SMC
D9, D11: BAV99; SOT-23
F1, F2: 30A; Fuse_Littelfuse-NANO2-451_453
F3: 5A; Fuse_Littelfuse-NANO2-451_453
J2: XT30-F; AMASS_XT30U-F_1x02_P5.0mm_Vertical
J3, J7, J12, J13, J14, J15, J16: Conn_M; PinHeader_2x02_P2.00mm_Vertical_SMD
J4, J5, J6: XT30-M; AMASS_XT30U-M_1x02_P5.0mm_Vertical
L2: L; L_Wuerth_HCI-1040
L5: 10uH; L_VER2923
Q1, Q2, Q3, Q4, Q5, Q6: BSC070N10N; TDSON-8-1
R1, R2, R4, R5, R6, R7: R_Gate; R_0603_1608Metric
R3, R8, R9, R10: 2mR; R_2512_6332Metric
R11, R12, R13, R14: 4k7; R_0603_1608Metric
U1: UCC27201A; SOIC-8_3.9x4.9mm_P1.27mm
U2, U3: UCC27211; SOIC-8_3.9x4.9mm_P1.27mm

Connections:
+10VA: C5.1, J3.3, R11.1, U1.1 (VDD)
+10VB: C27.1, J7.3, R13.1, U2.1 (VDD)
+10VC: C25.1, J16.4, U3.1 (VDD)
/A_HB: C7.1, D2.1 (K), R12.2, U1.2 (HB)
/A_HG: Q1.4 (G), R1.2
/A_HI: J3.2, U1.5 (HI)
/A_LG: Q2.4 (G), R2.2
/A_LI: J3.1, U1.6 (LI)
/A_SW: C7.2, C28.2, D2.2 (A), L5.1, Q1.1 (S), Q1.2 (S), Q1.3 (S), Q2.5 (D), U1.4 (HS)
/B_HB: C8.1, D10.1 (K), R14.2, U2.2 (HB)
/B_HG: Q3.4 (G), R4.2
/B_HI: J7.2, U2.5 (HI)
/B_LG: Q4.4 (G), R5.2
/B_LI: J7.1, U2.6 (LI)
/B_SW: C8.2, C12.2, D10.2 (A), L5.2, Q3.1 (S), Q3.2 (S), Q3.3 (S), Q4.5 (D), U2.4 (HS)
/C_HB: C26.1, U3.2 (HB)
/C_HG: Q5.4 (G), R6.2
/C_HI: J15.2, U3.5 (HI)
/C_LG: Q6.4 (G), R7.2
/C_LI: J15.4, U3.6 (LI)
/C_SW: C26.2, L2.1, Q5.1 (S), Q5.2 (S), Q5.3 (S), Q6.5 (D), U3.4 (HS)
A_POWER: C1.2, J12.4, Q1.5 (D), R9.2
A_POWER_CS: C13.1, C14.1, C15.2, C16.2, C17.2, C18.2, D5.1 (A1), F1.2, J12.1, J12.3, R9.1
B_POWER: C2.2, J13.2, Q3.5 (D), R10.1
B_POWER_CS: C19.2, C20.2, C21.2, C22.2, C23.1, C24.1, D6.1 (A1), F2.1, J13.1, J13.3, J16.2, R3.2, R10.2
C_POWER: C11.1, C30.1, C31.1, D1.1 (A1), F3.2, J15.1, Q5.5 (D)
C_POWER_OUT: C3.1, C4.1, C6.1, J16.1, L2.2, R3.1
GND: C1.1, C2.1, C3.2, C4.2, C5.2, C6.2, C11.2, C13.2, C14.2, C15.1, C16.1, C17.1, C18.1, C19.1, C20.1, C21.1, C22.1, C23.2, C24.2, C25.2, C27.2, C30.2, C31.2, D1.2 (A2), D5.2 (A2), D6.2 (A2), J2.1, J3.4, J4.1, J5.1, J6.1, J7.4, J12.2, J13.4, J14.3, J14.4, J15.3, J16.3, Q2.1 (S), Q2.2 (S), Q2.3 (S), Q4.1 (S), Q4.2 (S), Q4.3 (S), Q6.1 (S), Q6.2 (S), Q6.3 (S), U1.7 (VSS), U2.7 (VSS), U3.7 (VSS)
unnamed: C12.1, D11.3 (K)
unnamed: C28.1, D9.3 (K)
unnamed: D9.2 (A), R14.1
unnamed: D9.1 (K), R13.2
unnamed: D11.2 (A), R12.1
unnamed: D11.1 (K), R11.2
unnamed: F3.1, J6.2
unnamed: R1.1, U1.3 (HO)
unnamed: R2.1, U1.8 (LO)
unnamed: R4.1, U2.3 (HO)
unnamed: R5.1, U2.8 (LO)
unnamed: R6.1, U3.3 (HO)
unnamed: R7.1, U3.8 (LO)
V_CAPARR: F2.2, J4.2
V_CHASSIS: F1.1, J2.2, J14.2, R8.2
V_REFEREE: J5.2, J14.1, R8.1

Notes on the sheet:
UCC27201A SLM27211

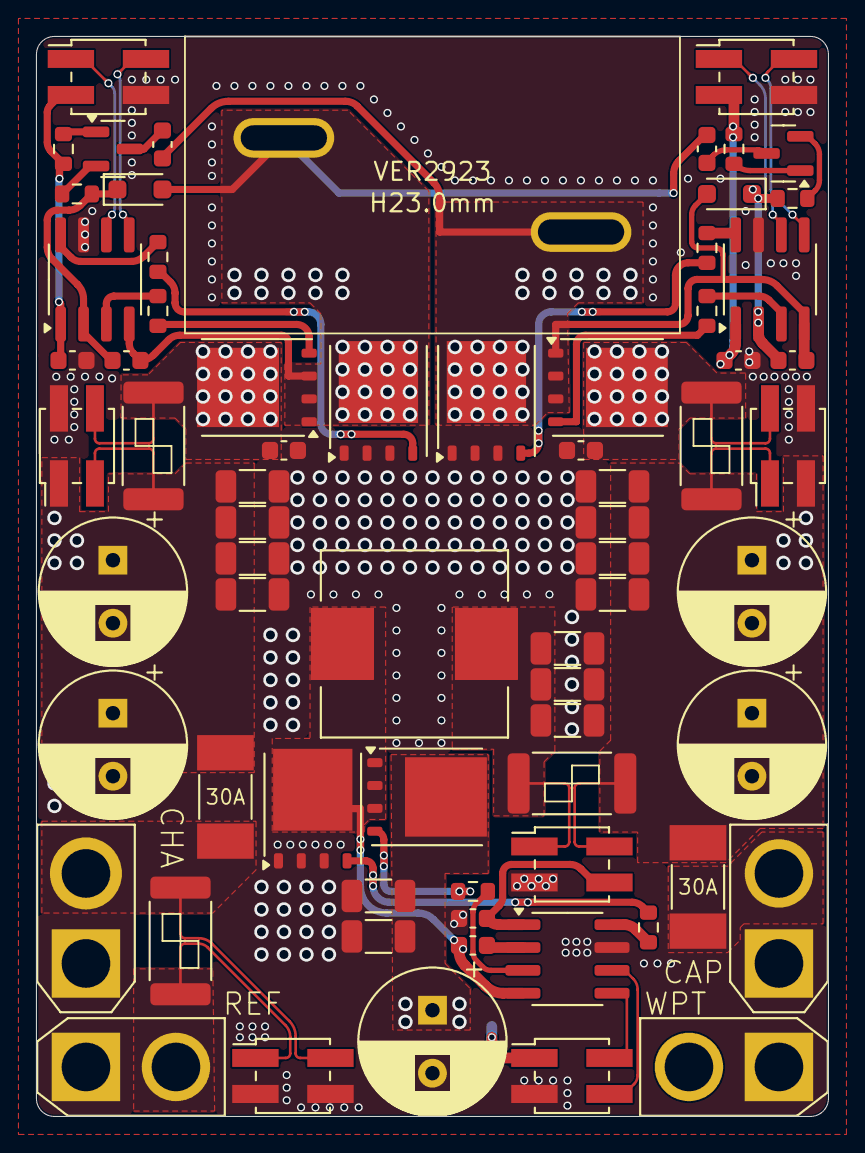
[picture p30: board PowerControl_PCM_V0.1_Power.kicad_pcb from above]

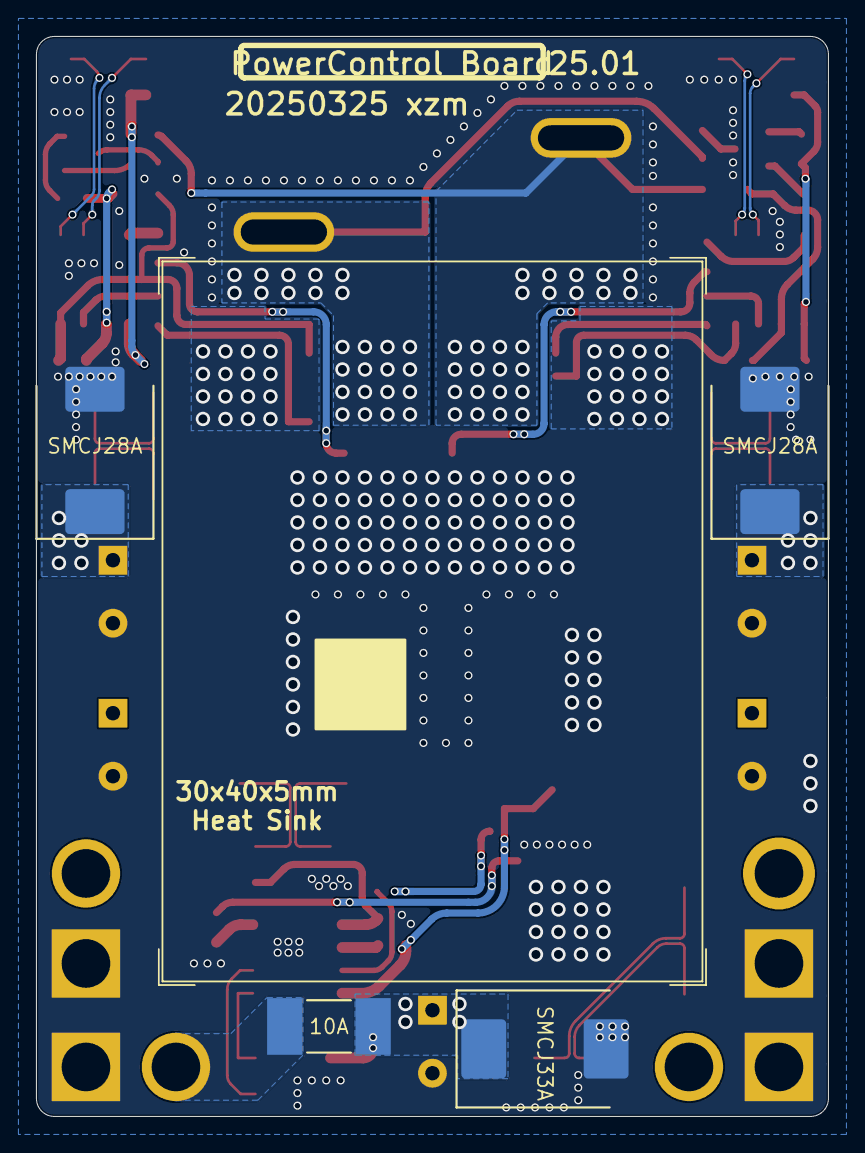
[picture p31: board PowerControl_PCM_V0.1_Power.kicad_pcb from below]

Board: 2 copper layers, 44.0 x 60.0 mm, 74 parts (4 on the bottom side), 44 nets.

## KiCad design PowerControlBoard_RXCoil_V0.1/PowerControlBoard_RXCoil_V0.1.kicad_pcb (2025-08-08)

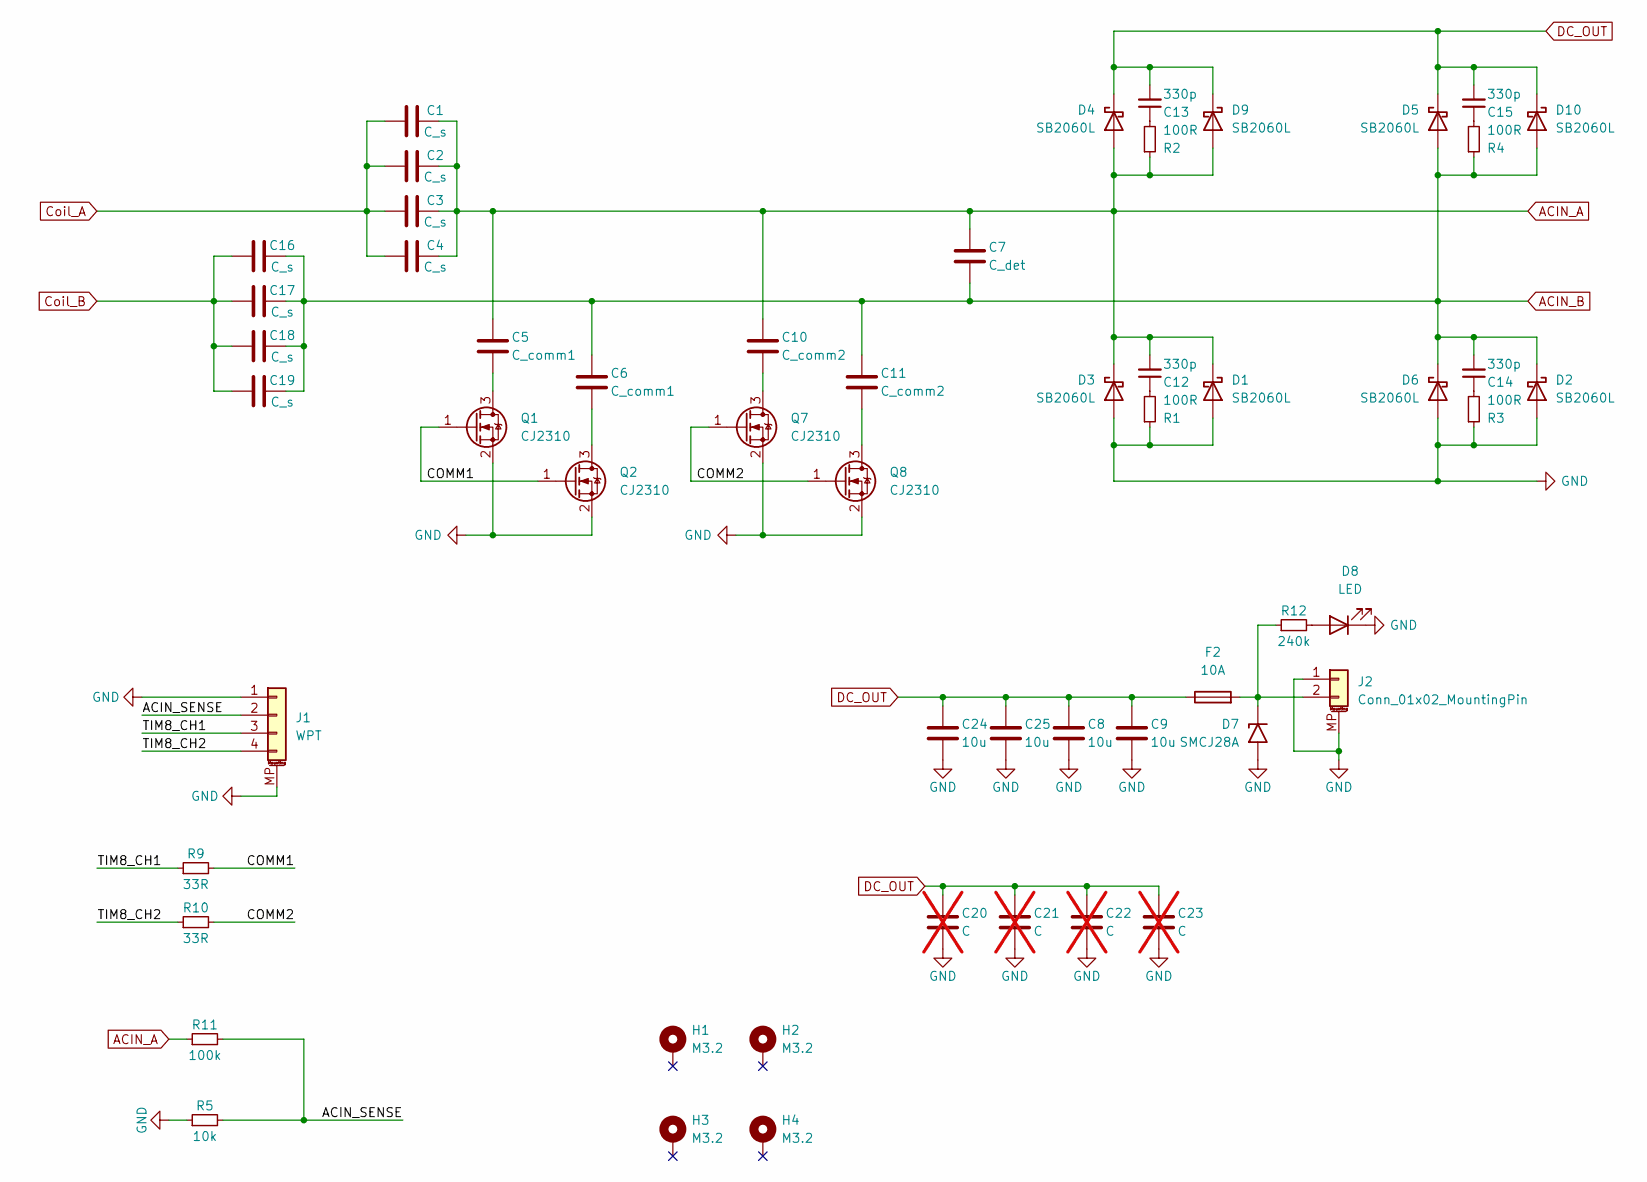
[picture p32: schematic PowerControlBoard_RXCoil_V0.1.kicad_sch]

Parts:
C1, C2, C3, C4, C16, C17, C18, C19: C_s; C_1206_3216Metric
C5, C6: C_comm1; C_1206_3216Metric
C7: C_det; C_1206_3216Metric
C8, C9, C24, C25: 10u; C_1206_3216Metric
C10, C11: C_comm2; C_1206_3216Metric
C12, C13, C14, C15: 330p; C_0603_1608Metric
C20, C21, C22, C23: C; C_1210_3225Metric; not fitted
D1, D2, D3, D4, D5, D6, D9, D10: SB2060L; D_PowerDI-5_3D
D7: SMCJ28A; D_SMC
D8: LED; LED_0603_1608Metric
F2: 10A; Fuseholder_Littelfuse_Nano2_157x
H1, H2, H3, H4: M3.2; MountingHole_3.2mm_M3_DIN965_Pad
J1: WPT; JST_GH_SM04B-GHS-TB_1x04-1MP_P1.25mm_Horizontal
J2: Conn_01x02_MountingPin; AMASS_XT30PW-F_Horizontal
Q1, Q2, Q7, Q8: CJ2310; SOT-23
R1, R2, R3, R4: 100R; R_0603_1608Metric
R5: 10k; R_0603_1608Metric
R9, R10: 33R; R_0603_1608Metric
R11: 100k; R_0603_1608Metric
R12: 240k; R_0603_1608Metric

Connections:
/ACIN_SENSE: J1.2, R5.2, R11.2
/COMM1: Q1.1 (G), Q2.1 (G), R9.2
/COMM2: Q7.1 (G), Q8.1 (G), R10.2
/TIM8_CH1: J1.3, R9.1
/TIM8_CH2: J1.4, R10.1
ACIN_A: C1.2, C2.2, C3.2, C4.2, C5.1, C7.1, C10.1, C12.2, D1.1 (K), D3.1 (K), D4.2 (A), D9.2 (A), R2.1, R11.1
ACIN_B: C6.1, C7.2, C11.1, C14.2, C16.2, C17.2, C18.2, C19.2, D2.1 (K), D5.2 (A), D6.1 (K), D10.2 (A), R4.1
Coil_A: C1.1, C2.1, C3.1, C4.1
Coil_B: C16.1, C17.1, C18.1, C19.1
DC_OUT: C8.1, C9.1, C13.2, C15.2, C20.1, C21.1, C22.1, C23.1, C24.1, C25.1, D4.1 (K), D5.1 (K), D9.1 (K), D10.1 (K), F2.1
GND: C8.2, C9.2, C20.2, C21.2, C22.2, C23.2, C24.2, C25.2, D1.2 (A), D2.2 (A), D3.2 (A), D6.2 (A), D7.2 (A2), D8.1 (K), J1.1, J1.MP (MountPin), J2.1, J2.MP (MountPin), Q1.2 (S), Q2.2 (S), Q7.2 (S), Q8.2 (S), R1.1, R3.1, R5.1
unnamed: C12.1, R1.2
unnamed: C13.1, R2.2
unnamed: C14.1, R3.2
unnamed: C15.1, R4.2
unnamed: D7.1 (A1), F2.2, J2.2, R12.1
unnamed: D8.2 (A), R12.2
unnamed: C5.2, Q1.3 (D)
unnamed: C6.2, Q2.3 (D)
unnamed: C10.2, Q7.3 (D)
unnamed: C11.2, Q8.3 (D)

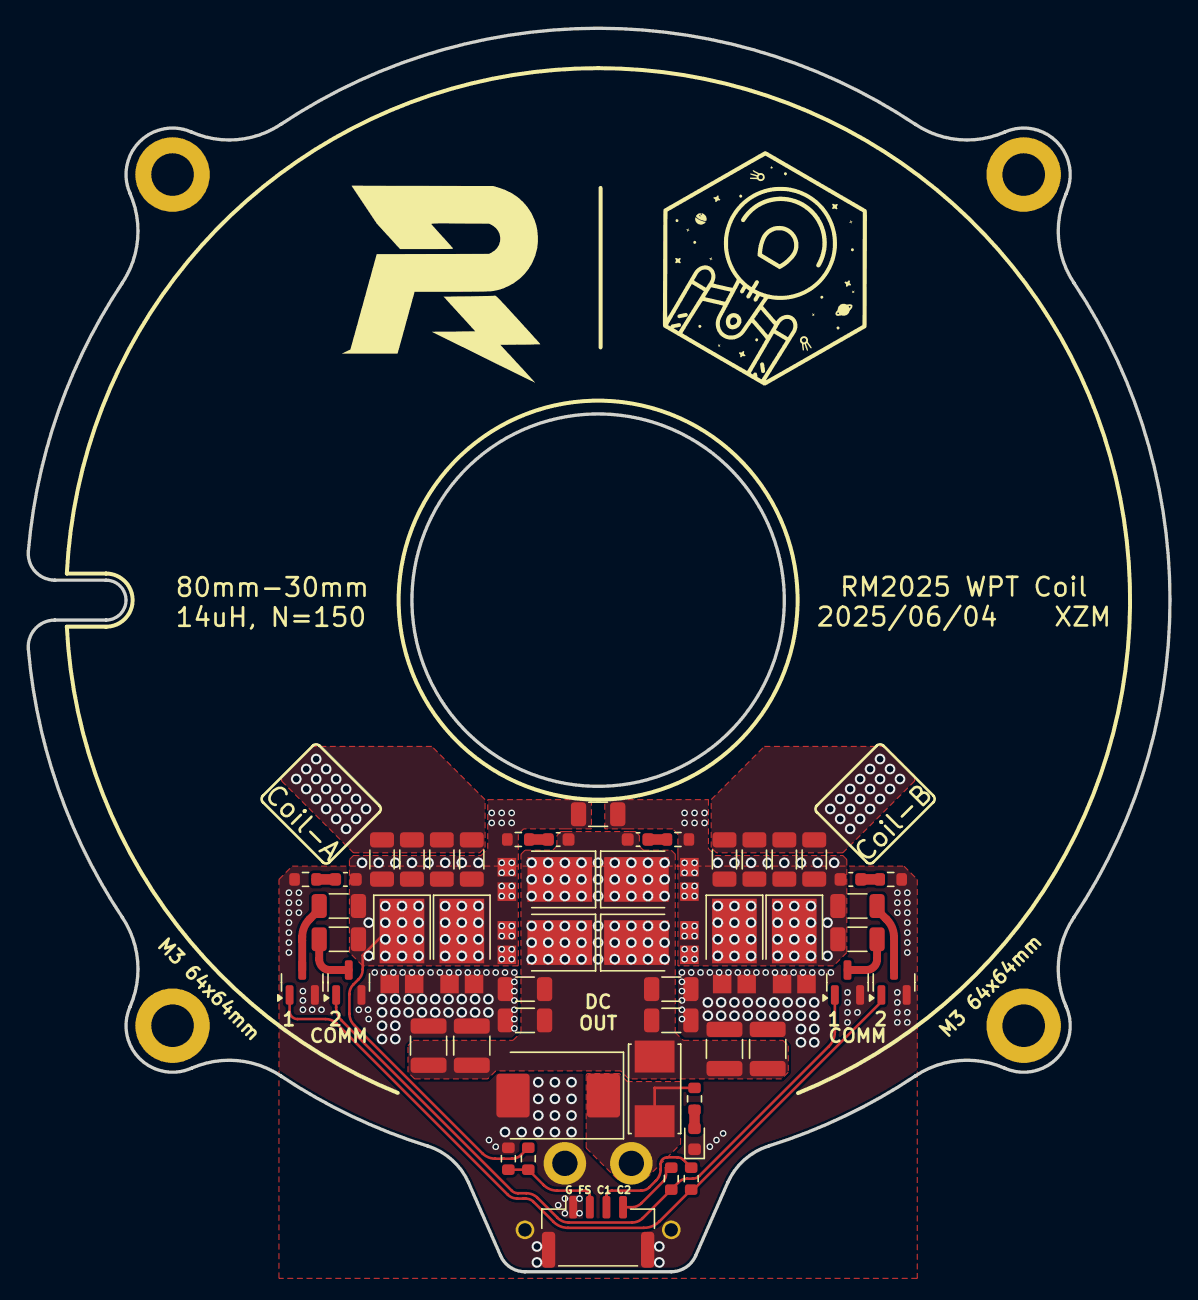
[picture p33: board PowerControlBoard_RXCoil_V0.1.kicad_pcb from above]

Board: 2 copper layers, 85.8 x 93.5 mm, 55 parts (1 on the bottom side), 21 nets.

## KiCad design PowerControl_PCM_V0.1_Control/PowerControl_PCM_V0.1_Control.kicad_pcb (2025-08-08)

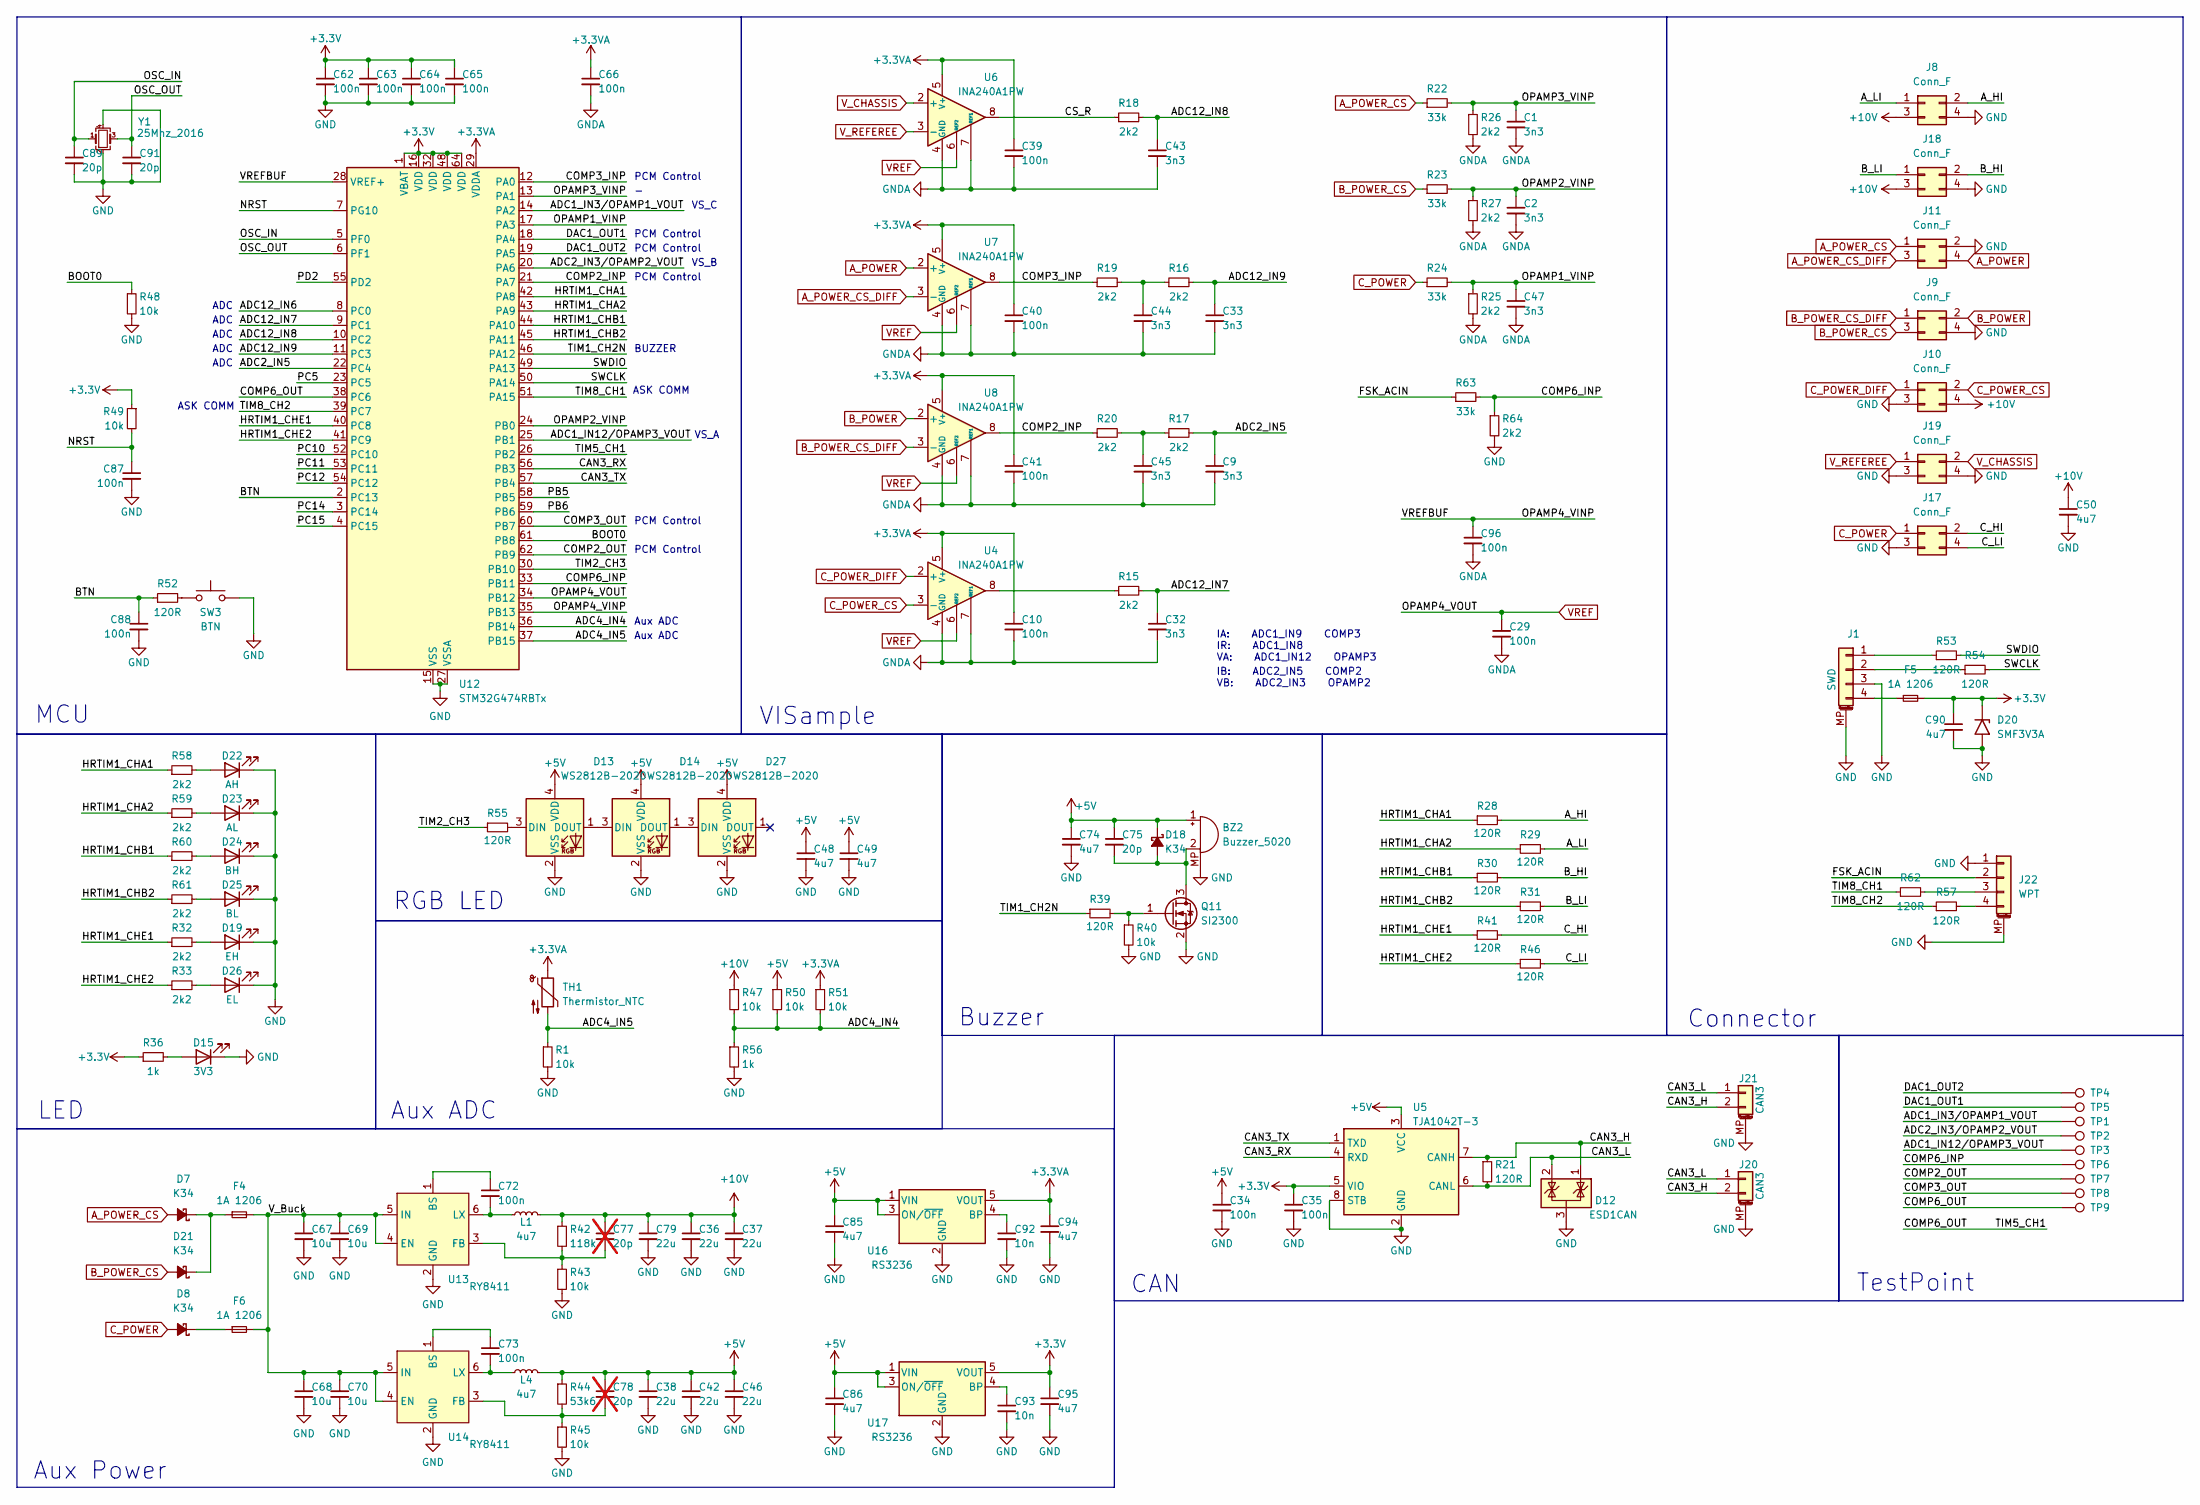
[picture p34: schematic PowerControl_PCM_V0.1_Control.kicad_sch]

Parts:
BZ2: Buzzer_5020
C1, C2, C9, C32, C33, C43, C44, C45, C47: 3n3; C_0603_1608Metric
C10, C29, C34, C35, C39, C40, C41, C62, C63, C64, C65, C66, C72, C73, C87, C88, C96: 100n; C_0603_1608Metric
C36, C37, C38, C42, C46, C79: 22u; C_0805_2012Metric
C48, C49, C50, C74, C85, C86, C90, C94, C95: 4u7; C_0603_1608Metric
C67, C68, C69, C70: 10u; C_1206_3216Metric
C75, C89, C91: 20p; C_0603_1608Metric
C77, C78: 20p; C_0603_1608Metric; not fitted
C92, C93: 10n; C_0603_1608Metric
D7, D8, D18, D21: K34; D_SMF
D12: ESD1CAN; SOT-23
D13, D14, D27: WS2812B-2020
D15: 3V3; LED_0603_1608Metric
D19: EH; LED_0603_1608Metric
D20: SMF3V3A; D_SMF
D22: AH; LED_0603_1608Metric
D23: AL; LED_0603_1608Metric
D24: BH; LED_0603_1608Metric
D25: BL; LED_0603_1608Metric
D26: EL; LED_0603_1608Metric
F4, F5, F6: 1A 1206; Fuse_1206_3216Metric
J1: SWD; Molex_PicoBlade_53261-0471_1x04-1MP_P1.25mm_Horizontal
J8, J9, J10, J11, J17, J18, J19: Conn_F; PinSocket_2x02_P2.00mm
J20, J21: CAN3; JST_GH_BM02B-GHS-TBT_1x02-1MP_P1.25mm_Vertical
J22: WPT; JST_GH_BM04B-GHS-TBT_1x04-1MP_P1.25mm_Vertical
L1, L4: 4u7; L_Sunlord_SWPA3015S
Q11: SI2300; SOT-23
R1, R40, R43, R45, R47, R48, R49, R50, R51: 10k; R_0603_1608Metric
R15, R16, R17, R18, R19, R20, R25, R26, R27, R32, R33, R58, R59, R60, R61, R64: 2k2; R_0603_1608Metric
R21, R28, R29, R30, R31, R39, R41, R46, R52, R53, R54, R55, R57, R62: 120R; R_0603_1608Metric
R22, R23, R24, R63: 33k; R_0603_1608Metric
R36, R56: 1k; R_0603_1608Metric
R42: 118k; R_0603_1608Metric
R44: 53k6; R_0603_1608Metric
SW3: BTN; Button_PTS810
TH1: Thermistor_NTC; R_0603_1608Metric
TP1, TP2, TP3, TP4, TP5, TP6, TP7, TP8, TP9: TestPoint; TestPoint_Pad_D1.0mm
U4, U6, U7, U8: INA240A1PW; TSSOP-8_4.4x3mm_P0.65mm
U5: TJA1042T-3; SOIC-8_3.9x4.9mm_P1.27mm
U12: STM32G474RBTx; LQFP-64_10x10mm_P0.5mm
U13, U14: RY8411; SOT-23-6
U16, U17: RS3236; SOT-23-5
Y1: 25Mhz_2016; Crystal_SMD_2016

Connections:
+3.3V: C35.1, C62.1, C63.1, C64.1, C65.1, C90.1, C95.1, D20.1 (A1), F5.2, R36.1, R49.1, U5.5 (VIO), U12.1 (VBAT), U12.16 (VDD), U12.32 (VDD), U12.48 (VDD), U12.64 (VDD), U17.5 (VOUT)
+3.3VA: C10.1, C39.1, C40.1, C41.1, C66.1, C94.1, R51.1, TH1.1, U4.5 (V+), U6.5 (V+), U7.5 (V+), U8.5 (V+), U12.29 (VDDA), U16.5 (VOUT)
+5V: BZ2.1 (+), C34.1, C38.1, C42.1, C46.1, C48.1, C49.1, C74.1, C75.1, C78.1, C85.1, C86.1, D13.4 (VDD), D14.4 (VDD), D18.1 (K), D27.4 (VDD), L4.2, R44.1, R50.1, U5.3 (VCC), U16.1 (VIN), U16.3 (ON/~OFF), U17.1 (VIN), U17.3 (ON/~OFF)
+10V: C36.1, C37.1, C50.1, C77.1, C79.1, J8.3, J10.4, J18.3, L1.2, R42.1, R47.1
/ADC1_IN3/OPAMP1_VOUT: TP1.1, U12.14 (PA2)
/ADC1_IN12/OPAMP3_VOUT: TP3.1, U12.25 (PB1)
/ADC2_IN3/OPAMP2_VOUT: TP2.1, U12.20 (PA6)
/ADC2_IN5: C9.1, R17.2, U12.22 (PC4)
/ADC4_IN4: R47.2, R50.2, R51.2, R56.1, U12.36 (PB14)
/ADC4_IN5: R1.1, TH1.2, U12.37 (PB15)
/ADC12_IN6: U12.8 (PC0)
/ADC12_IN7: C32.1, R15.2, U12.9 (PC1)
/ADC12_IN8: C43.1, R18.2, U12.10 (PC2)
/ADC12_IN9: C33.1, R16.2, U12.11 (PC3)
/A_HI: J8.2, R28.2
/A_LI: J8.1, R29.2
/BOOT0: R48.1, U12.61 (PB8)
/BTN: C88.1, R52.1, U12.2 (PC13)
/B_HI: J18.2, R30.2
/B_LI: J18.1, R31.2
/CAN3_H: D12.1 (K), J20.2, J21.2, R21.1, U5.7 (CANH)
/CAN3_L: D12.2 (K), J20.1, J21.1, R21.2, U5.6 (CANL)
/CAN3_RX: U5.4 (RXD), U12.56 (PB3)
/CAN3_TX: U5.1 (TXD), U12.57 (PB4)
/COMP2_INP: R20.1, U8.8, U12.21 (PA7)
/COMP2_OUT: TP7.1, U12.62 (PB9)
/COMP3_INP: R19.1, U7.8, U12.12 (PA0)
/COMP3_OUT: TP8.1, U12.60 (PB7)
/COMP6_INP: R63.2, R64.1, TP6.1, U12.33 (PB11)
/COMP6_OUT: TP9.1, U12.26 (PB2), U12.38 (PC6)
/CS_R: R18.1, U6.8
/C_HI: J17.2, R41.2
/C_LI: J17.4, R46.2
/DAC1_OUT1: TP5.1, U12.18 (PA4)
/DAC1_OUT2: TP4.1, U12.19 (PA5)
/FSK_ACIN: J22.2, R63.1
/HRTIM1_CHA1: R28.1, R58.1, U12.42 (PA8)
/HRTIM1_CHA2: R29.1, R59.1, U12.43 (PA9)
/HRTIM1_CHB1: R30.1, R60.1, U12.44 (PA10)
/HRTIM1_CHB2: R31.1, R61.1, U12.45 (PA11)
/HRTIM1_CHE1: R32.1, R41.1, U12.40 (PC8)
/HRTIM1_CHE2: R33.1, R46.1, U12.41 (PC9)
/NRST: C87.1, R49.2, U12.7 (PG10)
/OPAMP1_VINP: C47.1, R24.2, R25.1, U12.17 (PA3)
/OPAMP2_VINP: C2.1, R23.2, R27.1, U12.24 (PB0)
/OPAMP3_VINP: C1.1, R22.2, R26.1, U12.13 (PA1)
/OPAMP4_VINP: C96.1, U12.28 (VREF+), U12.35 (PB13)
/OSC_IN: C89.1, U12.5 (PF0), Y1.1
/OSC_OUT: C91.1, U12.6 (PF1), Y1.3
/PB5: U12.58 (PB5)
/PB6: U12.59 (PB6)
/PC5: U12.23 (PC5)
/PC10: U12.52 (PC10)
/PC11: U12.53 (PC11)
/PC12: U12.54 (PC12)
/PC14: U12.3 (PC14)
/PC15: U12.4 (PC15)
/PD2: U12.55 (PD2)
/SWCLK: R54.2, U12.50 (PA14)
/SWDIO: R53.2, U12.49 (PA13)
/TIM1_CH2N: R39.1, U12.46 (PA12)
/TIM2_CH3: R55.1, U12.30 (PB10)
/TIM8_CH1: R62.1, U12.51 (PA15)
/TIM8_CH2: R57.1, U12.39 (PC7)
/V_Buck: C67.1, C68.1, C69.1, C70.1, F4.2, F6.2, U13.4 (EN), U13.5 (IN), U14.4 (EN), U14.5 (IN)
A_POWER: J11.4, U7.2 (+)
A_POWER_CS: D7.2 (A), J11.1, R22.1
A_POWER_CS_DIFF: J11.3, U7.3 (-)
B_POWER: J9.2, U8.2 (+)
B_POWER_CS: D21.2 (A), J9.3, R23.1
B_POWER_CS_DIFF: J9.1, U8.3 (-)
C_POWER: D8.2 (A), J17.1, R24.1
C_POWER_CS: J10.2, U4.3 (-)
C_POWER_DIFF: J10.1, U4.2 (+)
GND: BZ2.MP, C34.2, C35.2, C36.2, C37.2, C38.2, C42.2, C46.2, C48.2, C49.2, C50.2, C62.2, C63.2, C64.2, C65.2, C67.2, C68.2, C69.2, C70.2, C74.2, C79.2, C85.2, C86.2, C87.2, C88.2, C89.2, C90.2, C91.2, C92.2, C93.2, C94.2, C95.2, D12.3 (A), D13.2 (VSS), D14.2 (VSS), D15.1 (K), D19.1 (K), D20.2 (A2), D22.1 (K), D23.1 (K), D24.1 (K), D25.1 (K), D26.1 (K), D27.2 (VSS), J1.3, J1.MP (MountPin), J8.4, J9.4, J10.3, J11.2, J17.3, J18.4, J19.3, J19.4, J20.MP (MountPin), J21.MP (MountPin), J22.1, J22.MP (MountPin), Q11.2 (S), R1.2, R40.2, R43.2, R45.2, R48.2, R56.2, R64.2, SW3.2, U5.2 (GND), U5.8 (STB), U12.15 (VSS), U12.27 (VSSA), U12.31 (VSS), U12.47 (VSS), U12.63 (VSS), U13.2 (GND), U14.2 (GND), U16.2 (GND), U17.2 (GND), Y1.2, Y1.4
GNDA: C1.2, C2.2, C9.2, C10.2, C29.2, C32.2, C33.2, C39.2, C40.2, C41.2, C43.2, C44.2, C45.2, C47.2, C66.2, C96.2, R25.2, R26.2, R27.2, U4.1 (GND), U4.4 (GND), U4.7 (REF1), U6.1 (GND), U6.4 (GND), U6.7 (REF1), U7.1 (GND), U7.4 (GND), U7.7 (REF1), U8.1 (GND), U8.4 (GND), U8.7 (REF1)
unnamed: BZ2.2 (-), C75.2, D18.2 (A), Q11.3 (D)
unnamed: C44.1, R16.1, R19.2
unnamed: C45.1, R17.1, R20.2
unnamed: D8.1 (K), F6.1
unnamed: D13.3 (DIN), R55.2
unnamed: D13.1 (DOUT), D14.3 (DIN)
unnamed: D14.1 (DOUT), D27.3 (DIN)
unnamed: D15.2 (A), R36.2
unnamed: D19.2 (A), R32.2
unnamed: D7.1 (K), D21.1 (K), F4.1
unnamed: D22.2 (A), R58.2
unnamed: D23.2 (A), R59.2
unnamed: D24.2 (A), R60.2
unnamed: D25.2 (A), R61.2
unnamed: D26.2 (A), R33.2
unnamed: J1.1, R53.1
unnamed: J1.2, R54.1
unnamed: F5.1, J1.4
unnamed: J22.3, R62.2
unnamed: J22.4, R57.2
unnamed: Q11.1 (G), R39.2, R40.1
unnamed: R15.1, U4.8
unnamed: R52.2, SW3.1
unnamed: C72.1, U13.1 (BS)
unnamed: C77.2, R42.2, R43.1, U13.3 (FB)
unnamed: C72.2, L1.1, U13.6 (LX)
unnamed: C73.1, U14.1 (BS)
unnamed: C78.2, R44.2, R45.1, U14.3 (FB)
unnamed: C73.2, L4.1, U14.6 (LX)
unnamed: C92.1, U16.4 (BP)
unnamed: C93.1, U17.4 (BP)
VREF: C29.1, U4.6 (REF2), U6.6 (REF2), U7.6 (REF2), U8.6 (REF2), U12.34 (PB12)
V_CHASSIS: J19.2, U6.2 (+)
V_REFEREE: J19.1, U6.3 (-)

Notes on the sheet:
Aux ADC
VS_A
ADC
IA: ADC1_IN9 COMP3 IR: ADC1_IN8 VA: ADC1_IN12 OPAMP3
PCM Control
Buzzer
TestPoint
CAN
Connector
VS_C
BUZZER
VISample
IB: ADC2_IN5 COMP2 VB: ADC2_IN3 OPAMP2
ASK COMM
LED
RGB LED
Aux Power
VS_B
MCU

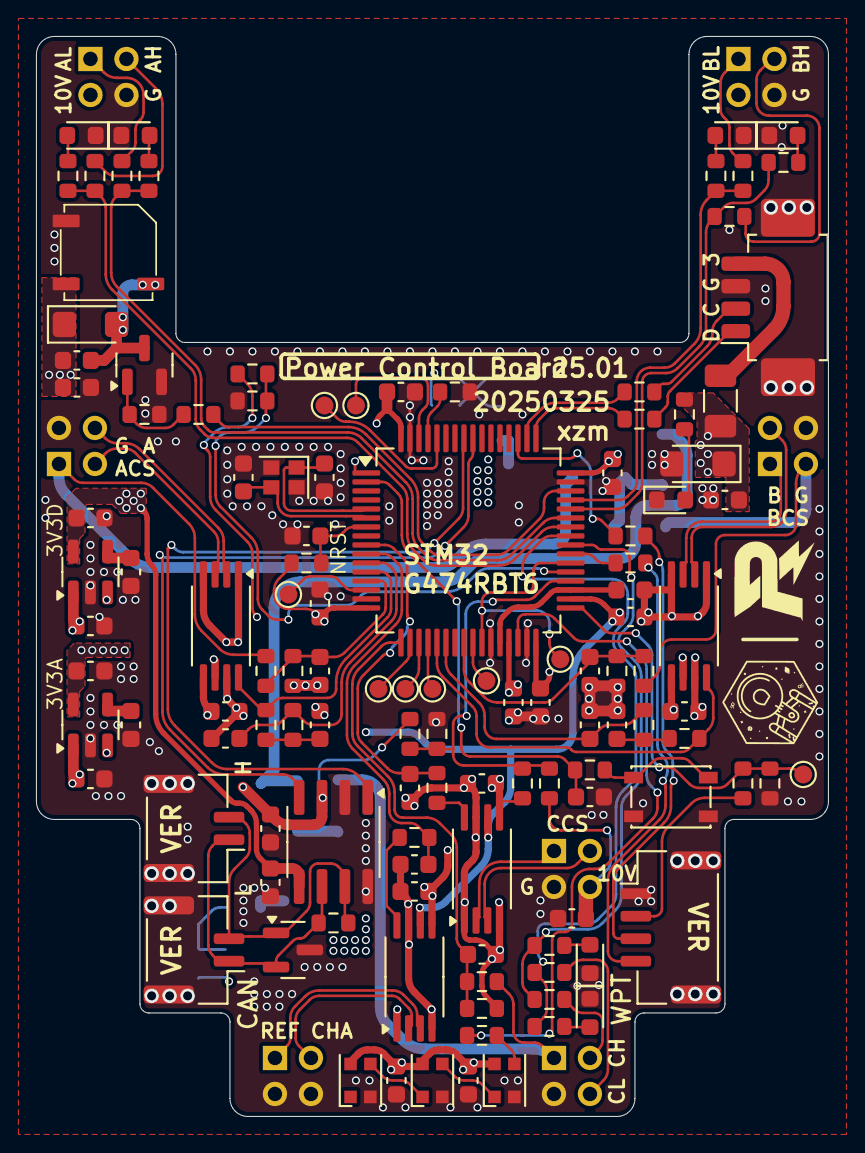
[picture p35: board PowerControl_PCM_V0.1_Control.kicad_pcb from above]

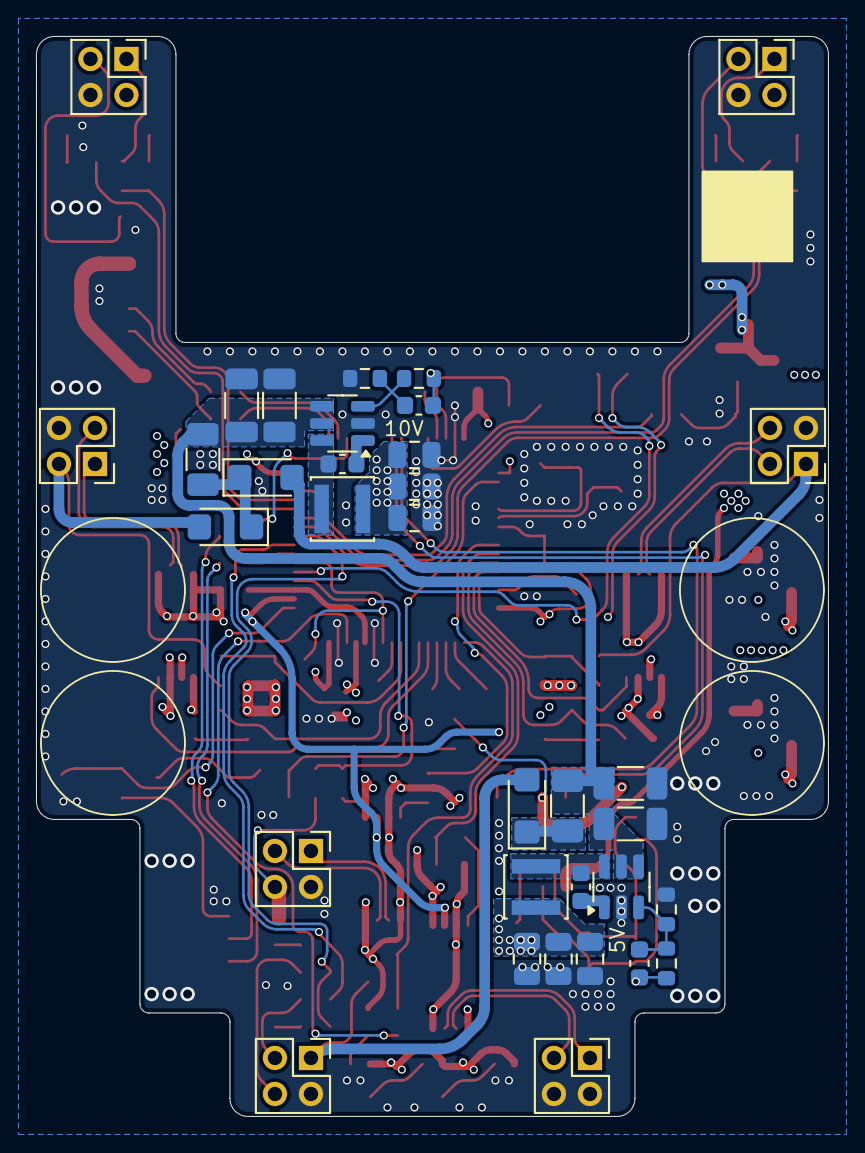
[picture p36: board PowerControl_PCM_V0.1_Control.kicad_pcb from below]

Board: 4 copper layers, 44.0 x 60.0 mm, 155 parts (34 on the bottom side), 100 nets.

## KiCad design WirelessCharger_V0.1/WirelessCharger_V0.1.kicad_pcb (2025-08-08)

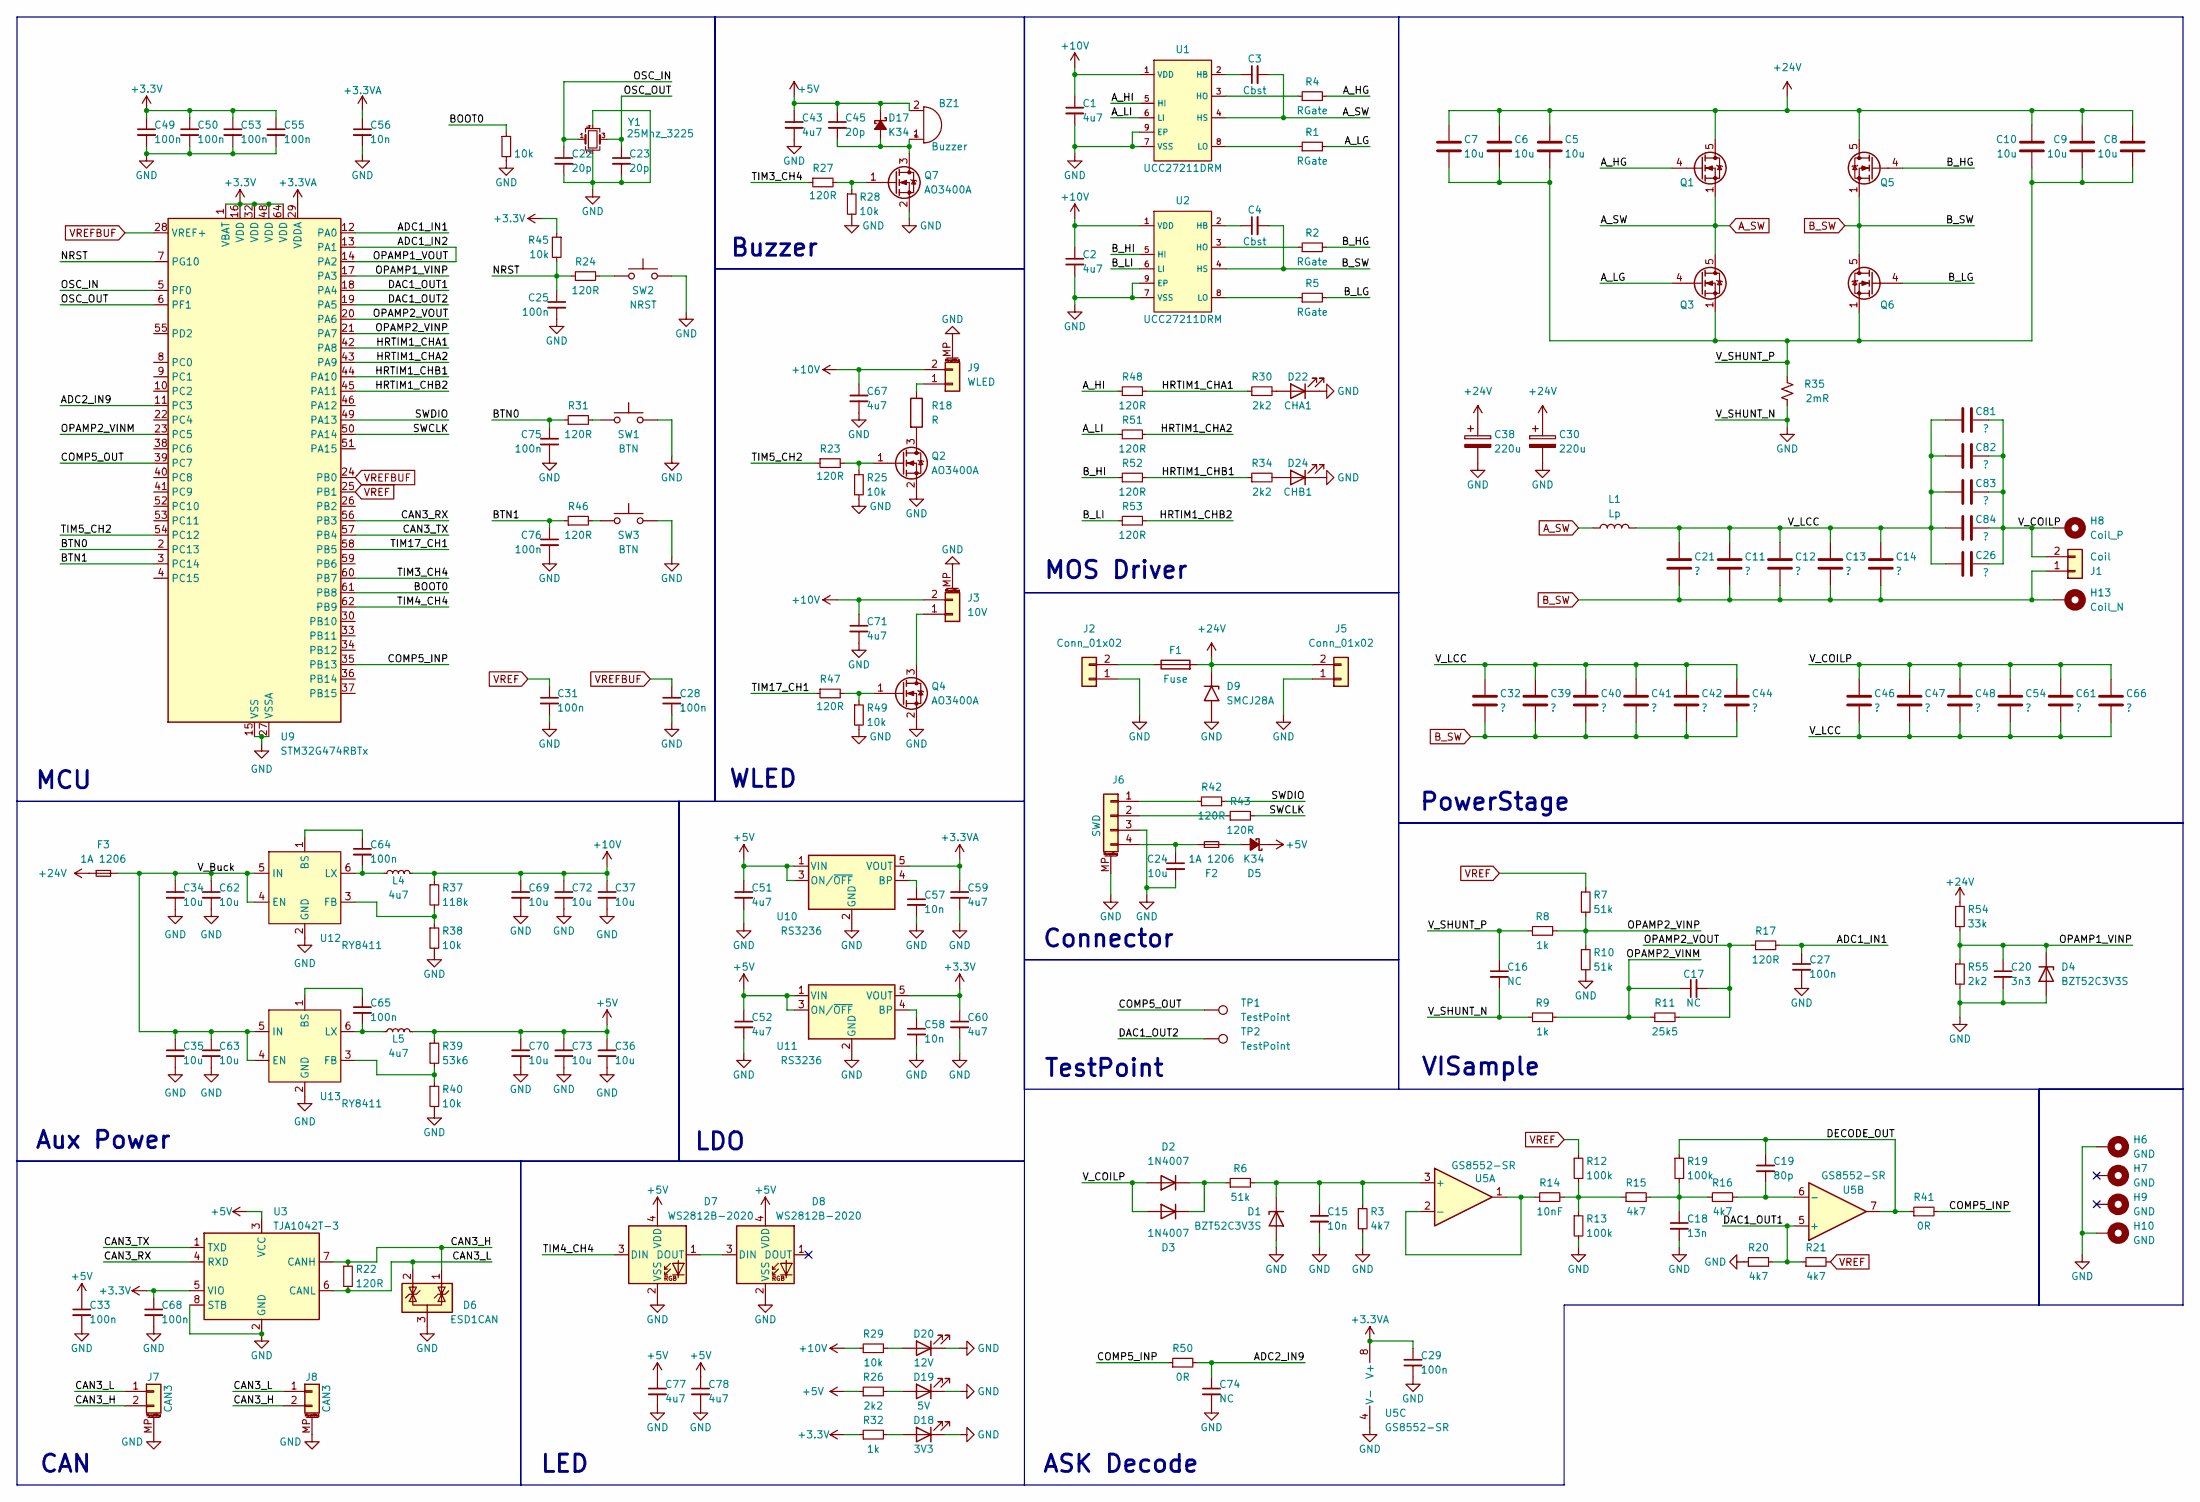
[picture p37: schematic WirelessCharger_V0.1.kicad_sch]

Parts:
BZ1: Buzzer; MLT-9032
C1, C2, C43, C51, C52, C59, C60, C67, C71, C77, C78: 4u7; C_0603_1608Metric
C3, C4: Cbst; C_0603_1608Metric
C5, C6, C7, C8, C9, C10, C34, C35, C62, C63: 10u; C_1206_3216Metric
C11, C12, C13, C14, C21, C26, C81, C82, C83, C84: ?; C_Rect_L11.0mm_W5.1mm_P10.00mm_MKT
C15, C56, C57, C58: 10n; C_0603_1608Metric
C16, C17, C74: NC; C_0603_1608Metric
C18: 13n; C_0603_1608Metric
C19: 80p; C_0603_1608Metric
C20: 3n3; C_0603_1608Metric
C22, C23, C45: 20p; C_0603_1608Metric
C24: 10u; C_0603_1608Metric
C25, C27, C28, C29, C31, C33, C49, C50, C53, C55, C64, C65, C68, C75, C76: 100n; C_0603_1608Metric
C30, C38: 220u; CP_Radial_D8.0mm_P3.50mm
C32, C39, C40, C41, C42, C44, C46, C47, C48, C54, C61, C66: ?; C_1206_3216Metric
C36, C37, C69, C70, C72, C73: 10u; C_0805_2012Metric
D1, D4: BZT52C3V3S; D_SOD-123F
D2, D3: 1N4007; D_SMF
D5, D17: K34; D_SMF
D6: ESD1CAN; SOT-23
D7, D8: WS2812B-2020
D9: SMCJ28A; D_SMC
D18: 3V3; LED_0603_1608Metric
D19: 5V; LED_0603_1608Metric
D20: 12V; LED_0603_1608Metric
D22: CHA1; LED_0603_1608Metric
D24: CHB1; LED_0603_1608Metric
F1: Fuse; Fuse_Littelfuse-NANO2-451_453
F2, F3: 1A 1206; Fuse_1206_3216Metric
H6, H7, H9, H10: GND; MountingHole_3.2mm_M3_DIN965_Pad
H8: Coil_P; TestPoint_Plated_Hole_D2.0mm
H13: Coil_N; TestPoint_Plated_Hole_D2.0mm
J1: Coil; AMASS_XT30U-F_Vertical
J2: Conn_01x02; AMASS_XT30U-M_Vertical
J3: 10V; JST_PH_B2B-PH-SM4-TB_1x02-1MP_P2.00mm_Vertical
J5: Conn_01x02; AMASS_XT30U-F_Vertical
J6: SWD; Molex_PicoBlade_53261-0471_1x04-1MP_P1.25mm_Horizontal
J7, J8: CAN3; JST_GH_BM02B-GHS-TBT_1x02-1MP_P1.25mm_Vertical
J9: WLED; JST_PH_B2B-PH-SM4-TB_1x02-1MP_P2.00mm_Vertical
L1: Lp; L_90125_3P
L4, L5: 4u7; L_Sunlord_SWPA3015S
Q1, Q3, Q5, Q6: BSC070N10NS3G; TDSON-8-1
Q2, Q4, Q7: AO3400A; SOT-23
R1, R2, R4, R5: RGate; R_0603_1608Metric
R3, R15, R16, R20, R21: 4k7; R_0603_1608Metric
R6, R7, R10: 51k; R_0603_1608Metric
R8, R9, R32: 1k; R_0603_1608Metric
R11: 25k5; R_0603_1608Metric
R12, R13, R19: 100k; R_0603_1608Metric
R14: 10nF; R_0603_1608Metric
R17, R22, R23, R24, R27, R31, R42, R43, R46, R47, R48, R51, R52, R53: 120R; R_0603_1608Metric
R18: R; R_1206_3216Metric
R25, R28, R29, R38, R40, R44, R45, R49: 10k; R_0603_1608Metric
R26, R30, R34, R55: 2k2; R_0603_1608Metric
R35: 2mR; R_2512_6332Metric
R37: 118k; R_0603_1608Metric
R39: 53k6; R_0603_1608Metric
R41, R50: 0R; R_0603_1608Metric
R54: 33k; R_0603_1608Metric
SW1, SW3: BTN; Button_PTS810
SW2: NRST; Button_PTS810
TP1, TP2: TestPoint; TestPoint_Pad_D1.5mm
U1, U2: UCC27211DRM; SOIC-8_3.9x4.9mm_P1.27mm
U3: TJA1042T-3; SOIC-8_3.9x4.9mm_P1.27mm
U5: GS8552-SR; SOIC-8_3.9x4.9mm_P1.27mm
U9: STM32G474RBTx; LQFP-64_10x10mm_P0.5mm
U10, U11: RS3236; SOT-23-5
U12, U13: RY8411; SOT-23-6
Y1: 25Mhz_3225; Crystal_SMD_2016

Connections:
+3.3V: C49.1, C50.1, C53.1, C55.1, C60.1, C68.1, R32.1, R45.1, U3.5 (VIO), U9.1 (VBAT), U9.16 (VDD), U9.32 (VDD), U9.48 (VDD), U9.64 (VDD), U11.5 (VOUT)
+3.3VA: C29.1, C56.1, C59.1, U5.8 (V+), U9.29 (VDDA), U10.5 (VOUT)
+5V: BZ1.2 (+), C33.1, C36.1, C43.1, C45.1, C51.1, C52.1, C70.1, C73.1, C77.1, C78.1, D5.1 (K), D7.4 (VDD), D8.4 (VDD), D17.1 (K), L5.2, R26.1, R39.1, U3.3 (VCC), U10.1 (VIN), U10.3 (ON/~OFF), U11.1 (VIN), U11.3 (ON/~OFF)
+10V: C1.1, C2.1, C37.1, C67.1, C69.1, C71.1, C72.1, J3.2, J9.2, L4.2, R29.1, R37.1, U1.1 (VDD), U2.1 (VDD)
+24V: C5.1, C6.1, C7.1, C8.1, C9.1, C10.1, C30.1, C38.1, D9.1 (A1), F1.2, F3.1, J5.2, Q1.5 (D), Q5.5 (D), R54.1
/ADC1_IN1: C27.1, R17.2, U9.12 (PA0)
/ADC1_IN2: U9.13 (PA1), U9.14 (PA2)
/ADC2_IN9: C74.1, R50.2, U9.11 (PC3)
/A_HG: Q1.4 (G), R4.2
/A_HI: R48.1, U1.5 (HI)
/A_LG: Q3.4 (G), R1.2
/A_LI: R51.1, U1.6 (LI)
/BOOT0: R44.1, U9.61 (PB8)
/BTN0: C75.1, R31.1, U9.2 (PC13)
/BTN1: C76.1, R46.1, U9.3 (PC14)
/B_HG: Q5.4 (G), R2.2
/B_HI: R52.1, U2.5 (HI)
/B_LG: Q6.4 (G), R5.2
/B_LI: R53.1, U2.6 (LI)
/CAN3_H: D6.1 (K), J7.2, J8.2, R22.1, U3.7 (CANH)
/CAN3_L: D6.2 (K), J7.1, J8.1, R22.2, U3.6 (CANL)
/CAN3_RX: U3.4 (RXD), U9.56 (PB3)
/CAN3_TX: U3.1 (TXD), U9.57 (PB4)
/COMP5_INP: R41.2, R50.1, U9.35 (PB13)
/COMP5_OUT: TP1.1, U9.39 (PC7)
/DAC1_OUT1: R20.2, R21.1, U5.5 (+), U9.18 (PA4)
/DAC1_OUT2: TP2.1, U9.19 (PA5)
/DECODE_OUT: C19.1, R19.1, R41.1, U5.7
/HRTIM1_CHA1: R30.1, R48.2, U9.42 (PA8)
/HRTIM1_CHA2: R51.2, U9.43 (PA9)
/HRTIM1_CHB1: R34.1, R52.2, U9.44 (PA10)
/HRTIM1_CHB2: R53.2, U9.45 (PA11)
/NRST: C25.1, R24.1, R45.2, U9.7 (PG10)
/OPAMP1_VINP: C20.1, D4.1 (K), R54.2, R55.1, U9.17 (PA3)
/OPAMP2_VINM: C17.1, R9.2, R11.1, U9.23 (PC5)
/OPAMP2_VINP: R7.2, R8.2, R10.1, U9.21 (PA7)
/OPAMP2_VOUT: C17.2, R11.2, R17.1, U9.20 (PA6)
/OSC_IN: C22.1, U9.5 (PF0), Y1.1
/OSC_OUT: C23.1, U9.6 (PF1), Y1.3
/SWCLK: R43.2, U9.50 (PA14)
/SWDIO: R42.2, U9.49 (PA13)
/TIM3_CH4: R27.1, U9.60 (PB7)
/TIM4_CH4: D7.3 (DIN), U9.62 (PB9)
/TIM5_CH2: R23.1, U9.54 (PC12)
/TIM17_CH1: R47.1, U9.58 (PB5)
/V_Buck: C34.1, C35.1, C62.1, C63.1, F3.2, U12.4 (EN), U12.5 (IN), U13.4 (EN), U13.5 (IN)
/V_COILP: C26.2, C46.1, C47.1, C48.1, C54.1, C61.1, C66.1, C81.2, C82.2, C83.2, C84.2, D2.2 (A), D3.2 (A), H8.1, J1.2
/V_LCC: C11.1, C12.1, C13.1, C14.1, C21.1, C26.1, C32.1, C39.1, C40.1, C41.1, C42.1, C44.1, C46.2, C47.2, C48.2, C54.2, C61.2, C66.2, C81.1, C82.1, C83.1, C84.1, L1.1
/V_SHUNT_P: C5.2, C6.2, C7.2, C8.2, C9.2, C10.2, C16.1, Q3.1 (S), Q3.2 (S), Q3.3 (S), Q6.1 (S), Q6.2 (S), Q6.3 (S), R8.1, R35.2
A_SW: C3.2, L1.2, Q1.1 (S), Q1.2 (S), Q1.3 (S), Q3.5 (D), U1.4 (HS)
B_SW: C4.2, C11.2, C12.2, C13.2, C14.2, C21.2, C32.2, C39.2, C40.2, C41.2, C42.2, C44.2, H13.1, J1.1, Q5.1 (S), Q5.2 (S), Q5.3 (S), Q6.5 (D), U2.4 (HS)
GND: C1.2, C2.2, C15.2, C16.2, C18.2, C20.2, C22.2, C23.2, C24.2, C25.2, C27.2, C28.2, C29.2, C30.2, C31.2, C33.2, C34.2, C35.2, C36.2, C37.2, C38.2, C43.2, C49.2, C50.2, C51.2, C52.2, C53.2, C55.2, C56.2, C57.2, C58.2, C59.2, C60.2, C62.2, C63.2, C67.2, C68.2, C69.2, C70.2, C71.2, C72.2, C73.2, C74.2, C75.2, C76.2, C77.2, C78.2, D1.2 (A), D4.2 (A), D6.3 (A), D7.2 (VSS), D8.2 (VSS), D9.2 (A2), D18.1 (K), D19.1 (K), D20.1 (K), D22.1 (K), D24.1 (K), H6.1, H10.1, J2.1, J3.MP (MountPin), J5.1, J6.3, J6.MP (MountPin), J7.MP (MountPin), J8.MP (MountPin), J9.MP (MountPin), Q2.2 (S), Q4.2 (S), Q7.2 (S), R3.2, R9.1, R10.2, R13.2, R20.1, R25.2, R28.2, R35.1, R38.2, R40.2, R44.2, R49.2, R55.2, SW1.2, SW2.2, SW3.2, U1.7 (VSS), U1.9 (EP), U2.7 (VSS), U2.9 (EP), U3.2 (GND), U3.8 (STB), U5.4 (V-), U9.15 (VSS), U9.27 (VSSA), U9.31 (VSS), U9.47 (VSS), U9.63 (VSS), U10.2 (GND), U11.2 (GND), U12.2 (GND), U13.2 (GND), Y1.2, Y1.4
unnamed: BZ1.1 (-), C45.2, D17.2 (A), Q7.3 (D)
unnamed: C18.1, R15.2, R16.1, R19.2
unnamed: C15.1, D1.1 (K), R3.1, R6.2, U5.3 (+)
unnamed: D2.1 (K), D3.1 (K), R6.1
unnamed: D5.2 (A), F2.2
unnamed: D7.1 (DOUT), D8.3 (DIN)
unnamed: D18.2 (A), R32.2
unnamed: D19.2 (A), R26.2
unnamed: D20.2 (A), R29.2
unnamed: D22.2 (A), R30.2
unnamed: D24.2 (A), R34.2
unnamed: F1.1, J2.2
unnamed: J3.1, Q4.3 (D)
unnamed: J6.1, R42.1
unnamed: J6.2, R43.1
unnamed: C24.1, F2.1, J6.4
unnamed: J9.1, R18.1
unnamed: Q2.3 (D), R18.2
unnamed: Q2.1 (G), R23.2, R25.1
unnamed: Q4.1 (G), R47.2, R49.1
unnamed: Q7.1 (G), R27.2, R28.1
unnamed: R12.2, R13.1, R14.2, R15.1
unnamed: R24.2, SW2.1
unnamed: R31.2, SW1.1
unnamed: R46.2, SW3.1
unnamed: C3.1, U1.2 (HB)
unnamed: R4.1, U1.3 (HO)
unnamed: R1.1, U1.8 (LO)
unnamed: C4.1, U2.2 (HB)
unnamed: R2.1, U2.3 (HO)
unnamed: R5.1, U2.8 (LO)
unnamed: R14.1, U5.1, U5.2 (-)
unnamed: C19.2, R16.2, U5.6 (-)
unnamed: C57.1, U10.4 (BP)
unnamed: C58.1, U11.4 (BP)
unnamed: C64.1, U12.1 (BS)
unnamed: R37.2, R38.1, U12.3 (FB)
unnamed: C64.2, L4.1, U12.6 (LX)
unnamed: C65.1, U13.1 (BS)
unnamed: R39.2, R40.1, U13.3 (FB)
unnamed: C65.2, L5.1, U13.6 (LX)
VREF: C31.1, R7.1, R12.1, R21.2, U9.25 (PB1)
VREFBUF: C28.1, U9.24 (PB0), U9.28 (VREF+)

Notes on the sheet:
VISample
TestPoint
LED
Aux Power
PowerStage
MCU
Connector
WLED
Buzzer
LDO
ASK Decode
MOS Driver
CAN

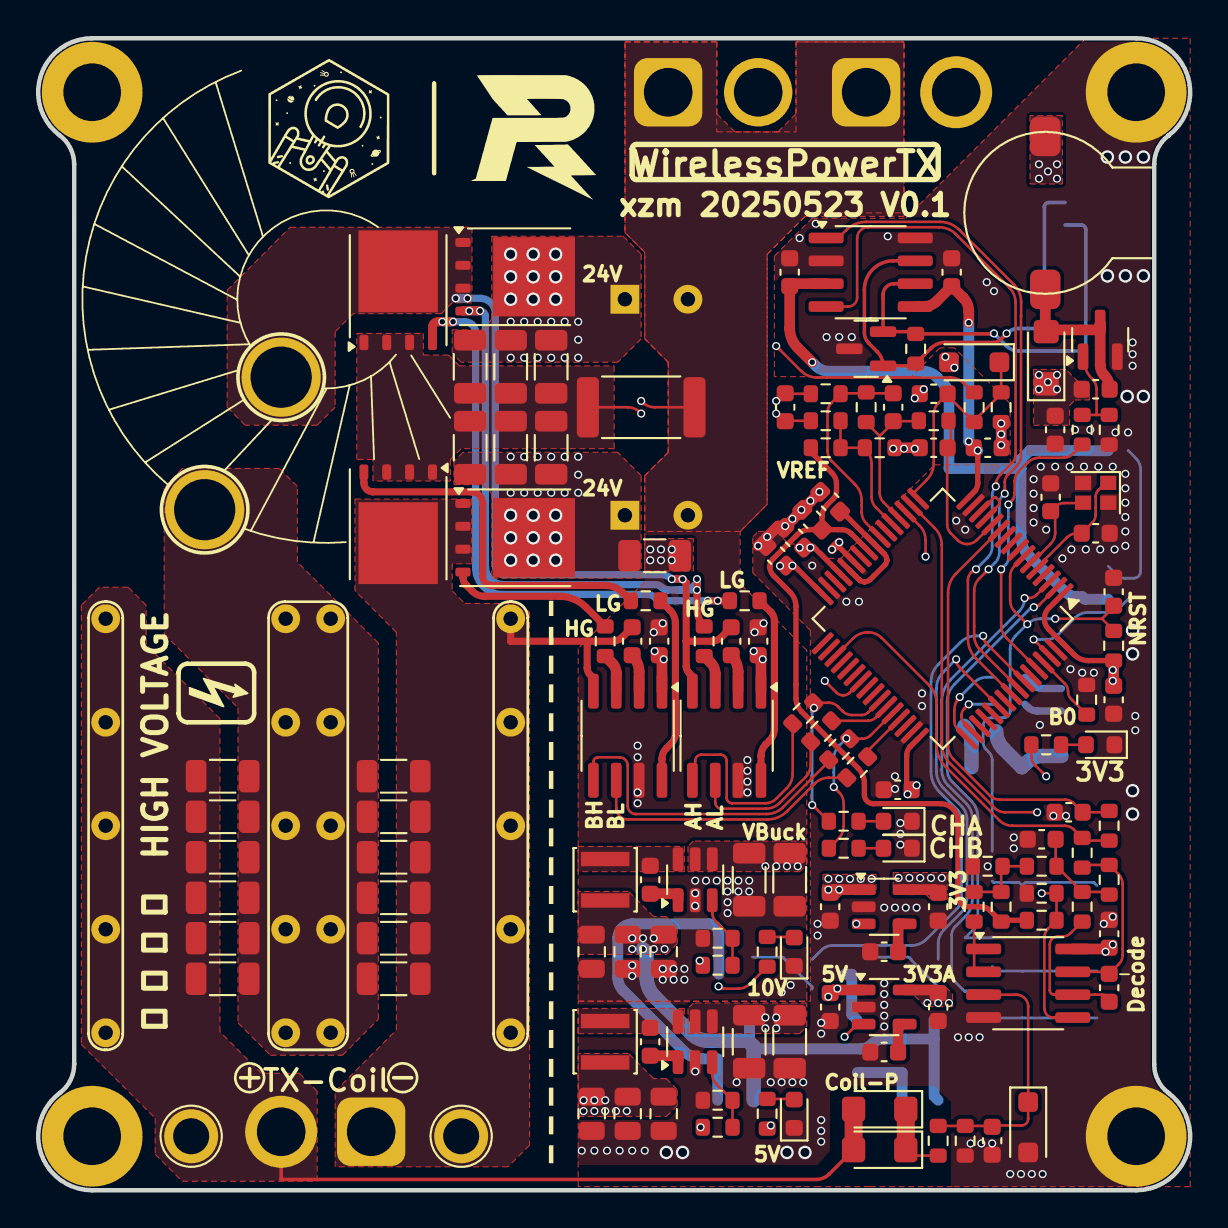
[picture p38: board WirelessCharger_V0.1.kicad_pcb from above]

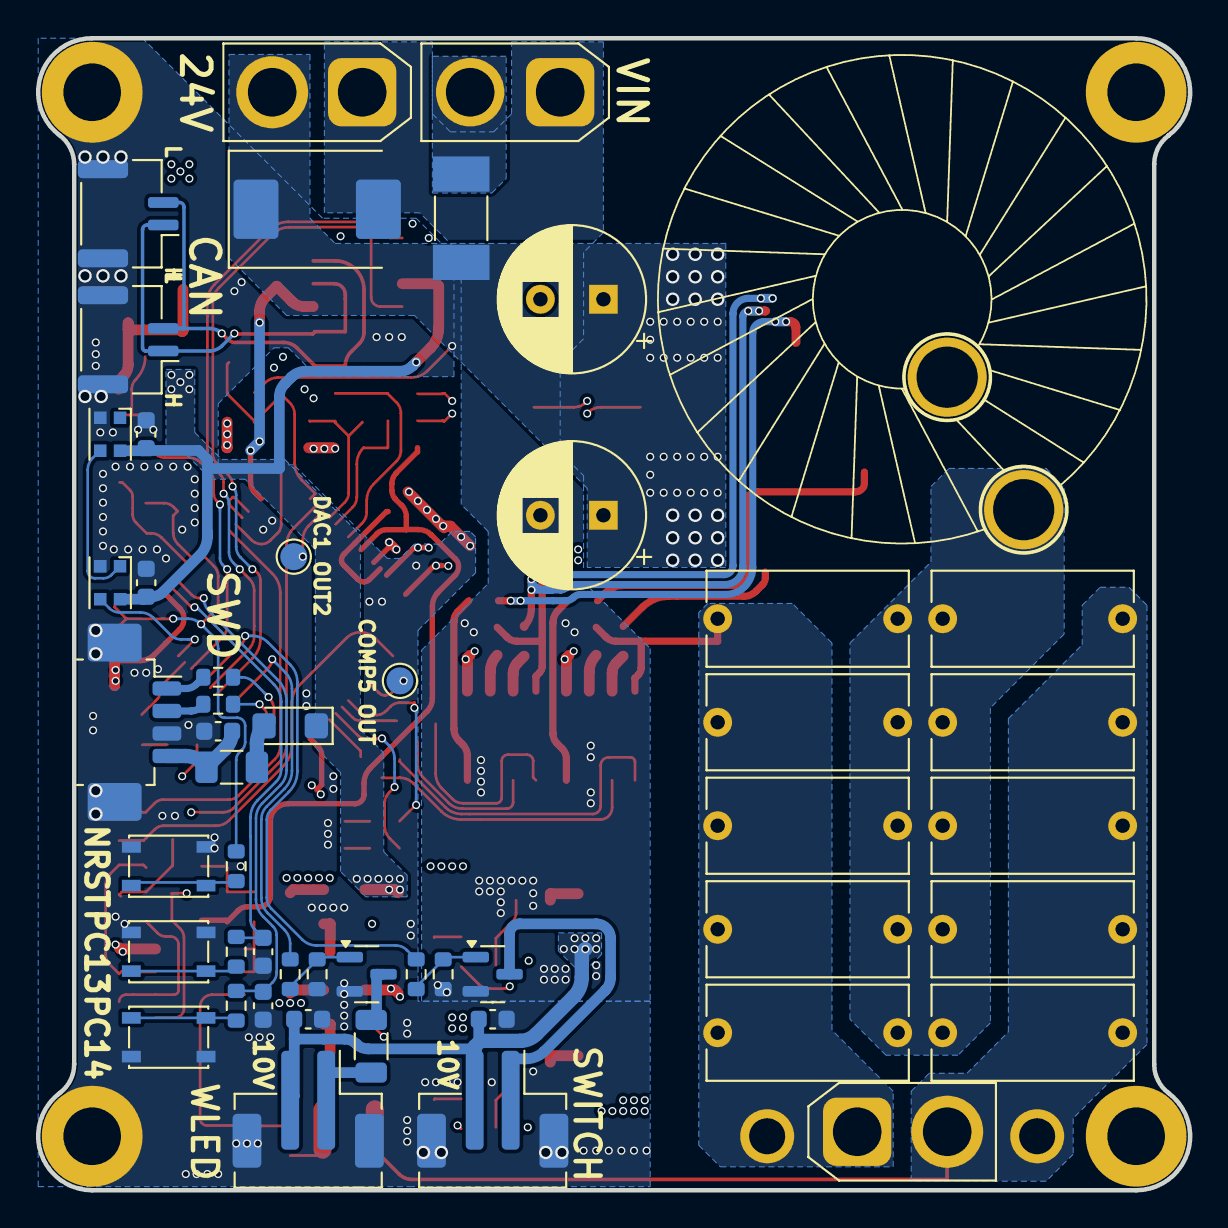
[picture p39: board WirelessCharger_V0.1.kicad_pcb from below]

Board: 4 copper layers, 64.0 x 64.0 mm, 193 parts (51 on the bottom side), 95 nets.

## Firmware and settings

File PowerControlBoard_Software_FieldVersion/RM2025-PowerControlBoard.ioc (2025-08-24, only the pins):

Mcu.UserName=STM32G474RBTx
PA0.Signal=COMP3_INP
PA1.Signal=OPAMP3_VINP
PA10.Signal=HRTIM1_CHB1
PA11.Signal=HRTIM1_CHB2
PA12.Signal=TIM1_CH2N
PA13.Signal=SYS_JTMS-SWDIO
PA14.Signal=SYS_JTCK-SWCLK
PA15.GPIO_Label=COMM1
PA15.Signal=GPIO_Output
PA2.Signal=SharedAnalog_PA2
PA3.Signal=OPAMP1_VINP
PA4.Signal=COMP_DAC11_group
PA5.Signal=COMP_DAC12_group
PA6.Signal=SharedAnalog_PA6
PA7.Signal=COMP2_INP
PA8.Signal=HRTIM1_CHA1
PA9.Signal=HRTIM1_CHA2
PB0.Signal=OPAMP2_VINP
PB1.Signal=SharedAnalog_PB1
PB10.Signal=S_TIM2_CH3
PB11.Signal=COMP6_INP
PB12.Signal=OPAMP4_VOUT
PB13.Signal=OPAMP4_VINP
PB14.Signal=ADC4_IN4
PB15.Signal=ADC4_IN5
PB2.Signal=S_TIM5_CH1
PB3.Signal=FDCAN3_RX
PB4.Signal=FDCAN3_TX
PB7.Signal=COMP3_OUT
PB9.Signal=COMP2_OUT
PC1.Signal=ADC2_IN7
PC13.GPIO_Label=BTN
PC13.Signal=GPIO_Input
PC2.Signal=ADC1_IN8
PC3.Signal=ADC1_IN9
PC4.Signal=ADC2_IN5
PC6.Signal=COMP6_OUT
PC7.GPIO_Label=COMM2
PC7.Signal=GPIO_Output
PC8.Signal=HRTIM1_CHE1
PC9.Signal=HRTIM1_CHE2
PF0-OSC_IN.Signal=RCC_OSC_IN
PF1-OSC_OUT.Signal=RCC_OSC_OUT

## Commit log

2025-08-08 外壳文件
2025-08-09 更新技术报告
2025-08-22 更新readme
2025-08-24 更新上场版代码
2025-08-24 更新Calibration
2025-10-06 增加校准excel
    [校准.xlsx]
